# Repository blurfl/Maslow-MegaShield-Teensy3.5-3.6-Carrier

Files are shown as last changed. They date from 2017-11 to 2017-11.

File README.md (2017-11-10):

# Maslow-MegaShield-Teensy3.5-3.6-Carrier
Carrier board to connect a Teensy 3.5 or 3.6 to a Maslow MegaShield motor control board
======================

***
Layout

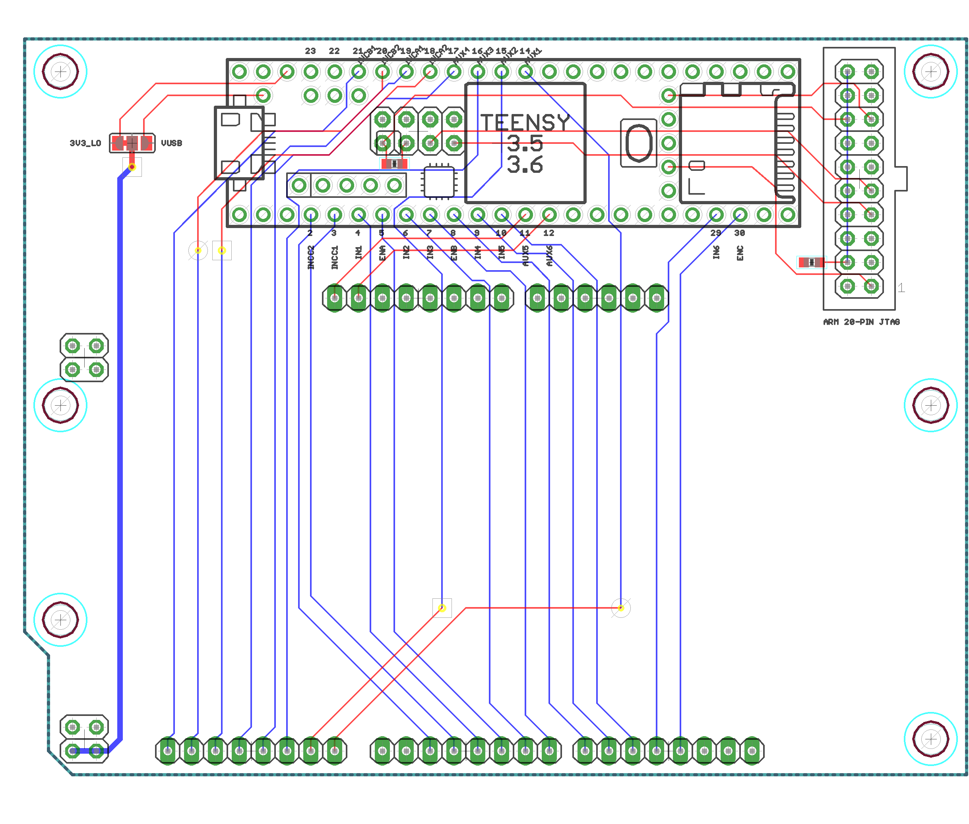
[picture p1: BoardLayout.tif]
Layout


***
Schematic

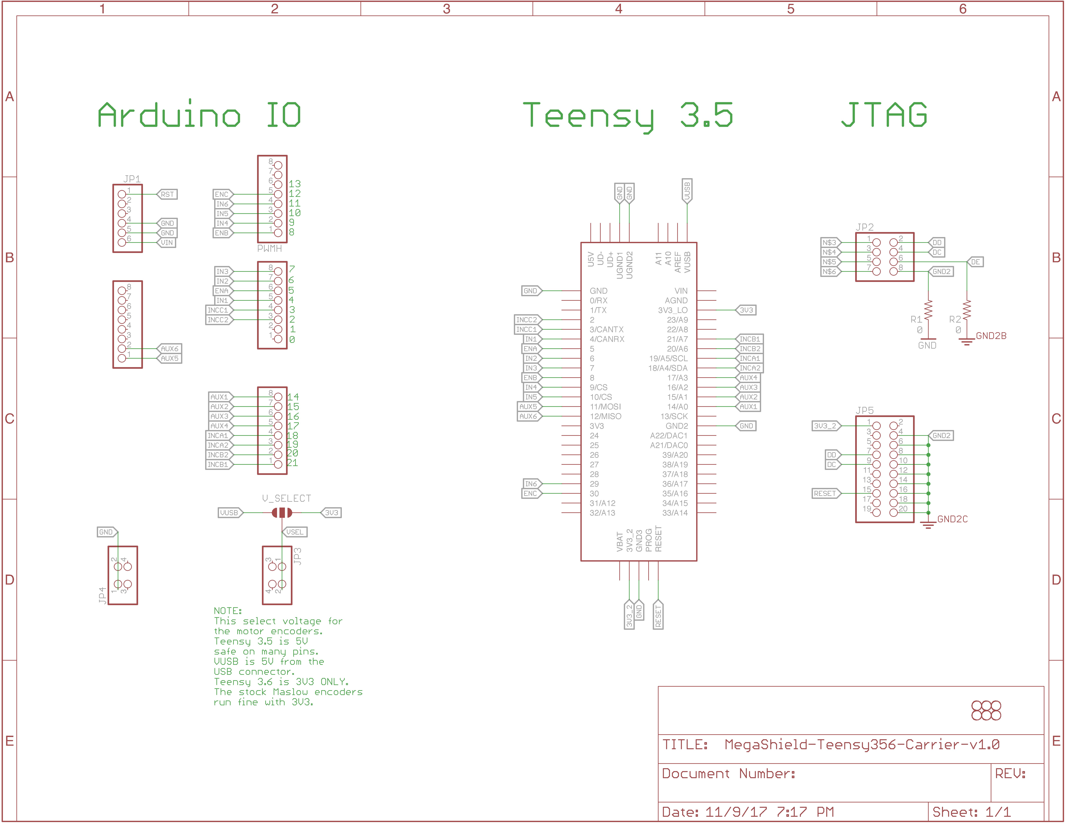
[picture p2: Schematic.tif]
Schematic


***
Notes

 Most of the pin assignments match the Arduino Mega. IN5 & IN6 were changed so that they would be PWM capable (for a different project). The AUX pins were re-arranged for convenience of layout. The board version detection was not implemented, as that would tie up four more gpio pins. 
 
 There is provision to choose the voltage used for the encoders, either the 5V from the USB connection or the 3V3 regulated by the Teensy. It is strapped for 3V3, and that seems to work well on the Teensy 3.5 I've tested. The Teensy 3.6 would be damaged by using more than 3V3 in its inputs.

 The JTAG parts are not tested.

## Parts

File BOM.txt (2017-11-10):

QUANTITY    DESCRIPTION     
4           PIN HEADER  1X8     
2           PIN HEADER  2X2
2           PIN HEADER  1X24

Note: some parts for future development not listed: 
R1, R2 JP2 and JP5 for JTAG
PIN HEADER 1x6 for JP1

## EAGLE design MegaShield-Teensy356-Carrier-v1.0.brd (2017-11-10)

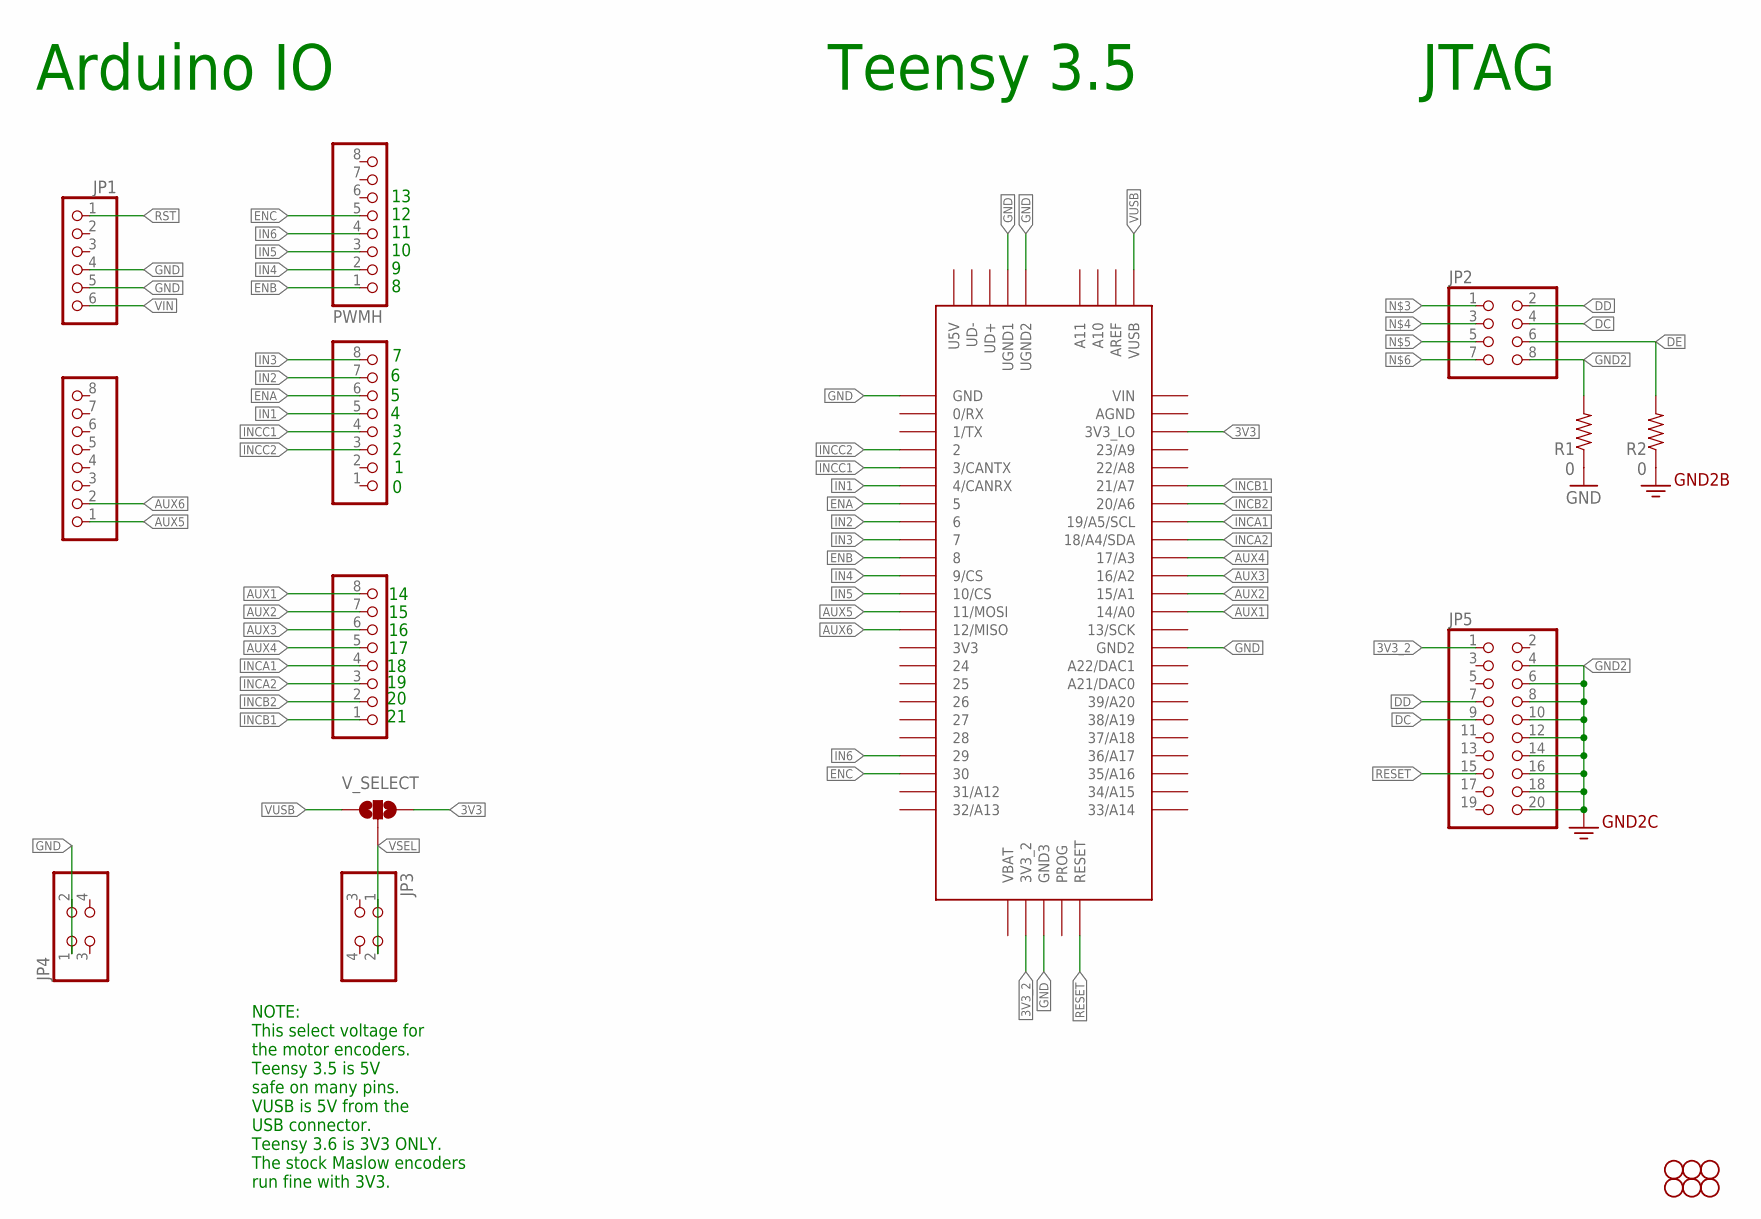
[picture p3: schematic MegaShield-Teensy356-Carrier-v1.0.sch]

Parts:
COMMUNICATION, COMMUNICATION1: PINHD-1X8; 1X08
H1, H2, H3, H4, H5, H6: STAND-OFF
JP1: PINHD-1X6; 1X06
JP2: PINHD-2X4; 2X04
JP3, JP4: PINHD-2X2; 2X02
JP5: PINHD-2X10; 2X10
PWMH: PINHD-1X8; 1X08
PWML: PINHD-1X8; 1X08
R1, R2: 0; 0603
U$15: TEENSY_3.5/3.6
V_SELECT: SOLDERJUMPER_2WAYT; SJ_2

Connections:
3V3: U$15.3V3_LO, V_SELECT.3
3V3_2: JP5.1, U$15.3V3_2
AUX1: COMMUNICATION.8, U$15.14/A0
AUX2: COMMUNICATION.7, U$15.15/A1
AUX3: COMMUNICATION.6, U$15.16/A2
AUX4: COMMUNICATION.5, U$15.17/A3
AUX5: COMMUNICATION1.1, U$15.11/MOSI
AUX6: COMMUNICATION1.2, U$15.12/MISO
DC: JP2.4, JP5.9
DD: JP2.2, JP5.7
DE: JP2.6, R2.2
ENA: PWML.6, U$15.5
ENB: PWMH.1, U$15.8
ENC: PWMH.5, U$15.30
GND: JP1.4, JP1.5, JP4.1, JP4.2, R1.1, U$15.GND, U$15.GND2, U$15.GND3, U$15.UGND1, U$15.UGND2
GND2: JP2.8, JP5.4, JP5.6, JP5.8, JP5.10, JP5.12, JP5.14, JP5.16, JP5.18, JP5.20, R1.2, R2.1
IN1: PWML.5, U$15.4/CANRX
IN2: PWML.7, U$15.6
IN3: PWML.8, U$15.7
IN4: PWMH.2, U$15.9/CS
IN5: PWMH.3, U$15.10/CS
IN6: PWMH.4, U$15.29
INCA1: COMMUNICATION.4, U$15.19/A5/SCL
INCA2: COMMUNICATION.3, U$15.18/A4/SDA
INCB1: COMMUNICATION.1, U$15.21/A7
INCB2: COMMUNICATION.2, U$15.20/A6
INCC1: PWML.4, U$15.3/CANTX
INCC2: PWML.3, U$15.2
RESET: JP5.15, U$15.RESET
RST: JP1.1
VIN: JP1.6
VSEL: JP3.1, JP3.2, V_SELECT.2
VUSB: U$15.VUSB, V_SELECT.1

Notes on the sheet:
Arduino IO
Teensy 3.5
NOTE: This select voltage for the motor encoders. Teensy 3.5 is 5V safe on many pins. VUSB is 5V from the USB connector. Teensy 3.6 is 3V3 ONLY. The stock Maslow encoders run fine with 3V3.
JTAG

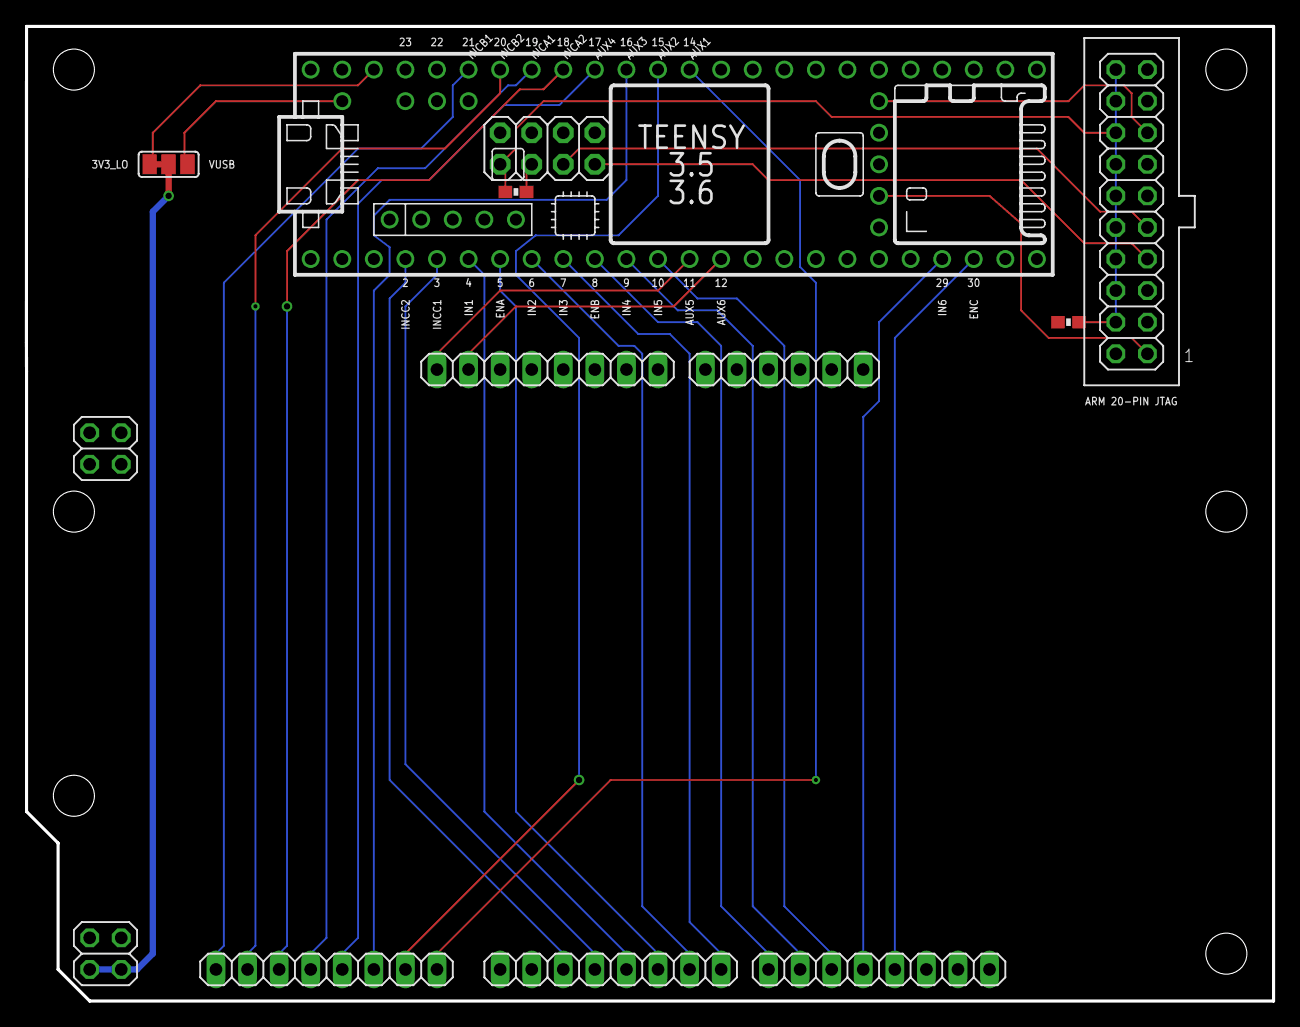
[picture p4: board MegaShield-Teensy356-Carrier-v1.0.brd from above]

Board: 2 copper layers, 100.3 x 78.4 mm, 19 parts (0 on the bottom side), 31 nets.

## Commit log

2017-11-10 Initial file import
    [MegaShield-Teensy356-Carrier-v1.0.brd, MegaShield-Teensy356-Carrier-v1.0.sch]
2017-11-10 ignore Copper settings file
    Copper app keeps settings alongside board and schematic

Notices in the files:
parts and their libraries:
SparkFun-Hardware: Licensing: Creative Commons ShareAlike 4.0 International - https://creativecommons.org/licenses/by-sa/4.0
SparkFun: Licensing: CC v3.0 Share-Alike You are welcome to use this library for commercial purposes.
